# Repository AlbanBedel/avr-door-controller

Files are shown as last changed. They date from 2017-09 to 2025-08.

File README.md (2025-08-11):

# AVR based wiegand door controller

This project is about building an open source physical access control
system for small communities and groups.

## Electronic

In this directory you will find the hardware design (schematics and PCB) for
a two door controller using an Arduino Nano. Its main features are:

* Can be powered with 12V or 24V.
* Support various setup for the door lock, the relay can be connected to
  12V, 24V or GND as normally open or as normally closed.
* An USB power supply to power additional devices such as an AP for network
  connectivity.
* Use RJ-45 connectors for the doors to allow standardizing the physical
  installation.

This design intentionally doesn't provide network connectivity for two reasons.
First we want to keep the device as cheap and reliable as possible. But most
importantly we want a secure system, implementing secure communication (SSL)
on a small micro-controller is not really possible. So instead of using dubious
Ethernet expansion boards we decided to only provide an USB interface and rely
on external devices running a full OS for access over the network.

### Pin out

	Pin | Function | T-568 A      | T-568 B      | Reader
	------------------------------------------------------
	  1 | Beep     | White Green  | White Orange | Yellow
	  2 | LED      | Green        | Orange       | Blue
	  3 | Status   | White Orange | White Green  |
	  4 | D1       | Blue         | Blue         | White
	  5 | D0       | White Blue   | White Blue   | Green
	  6 | Relay    | Orange       | Green        |
	  7 | 12V      | White Brown  | White Brown  | Red
	  8 | GND      | Brown        | Brown        | Black

## Firmware

In this directory you will find the firmware for the above hardware,
it supports both the Arduino Nano version 2 and version 3. We recommend using
version 3 as they have a much large EEPROM which allow for up to 200 access
records.

The firmware currently support:

* 26 bits wiegand RFID readers
* RFID reader with keypad for PIN
* Access with PIN only, card only or card + PIN
* TOTP and HOTP PIN
* Simple access records management over USB

The following is planned:

* Support external EEPROM for more access records
* 34 bits RFID cards

## Daemon

In this directory you will find a daemon that allow managing one or more
controllers using OpenWrt ubus. As OpenWrt include a JSON-RPC interface to ubus
this daemon allow to manage the controllers over the network using a JSON-RPC
interface.

## Client

In this directory you will find the client software to manage the controllers.
First is a tool (and python API) that allow to manage a controller, either over
USB or over JSON-RPC. This tool is pretty low level but make it easy to setup
a single controller with a couple of users. Then there is database backed tool
that allow to easily manage larger deployments with several controllers and many
users.

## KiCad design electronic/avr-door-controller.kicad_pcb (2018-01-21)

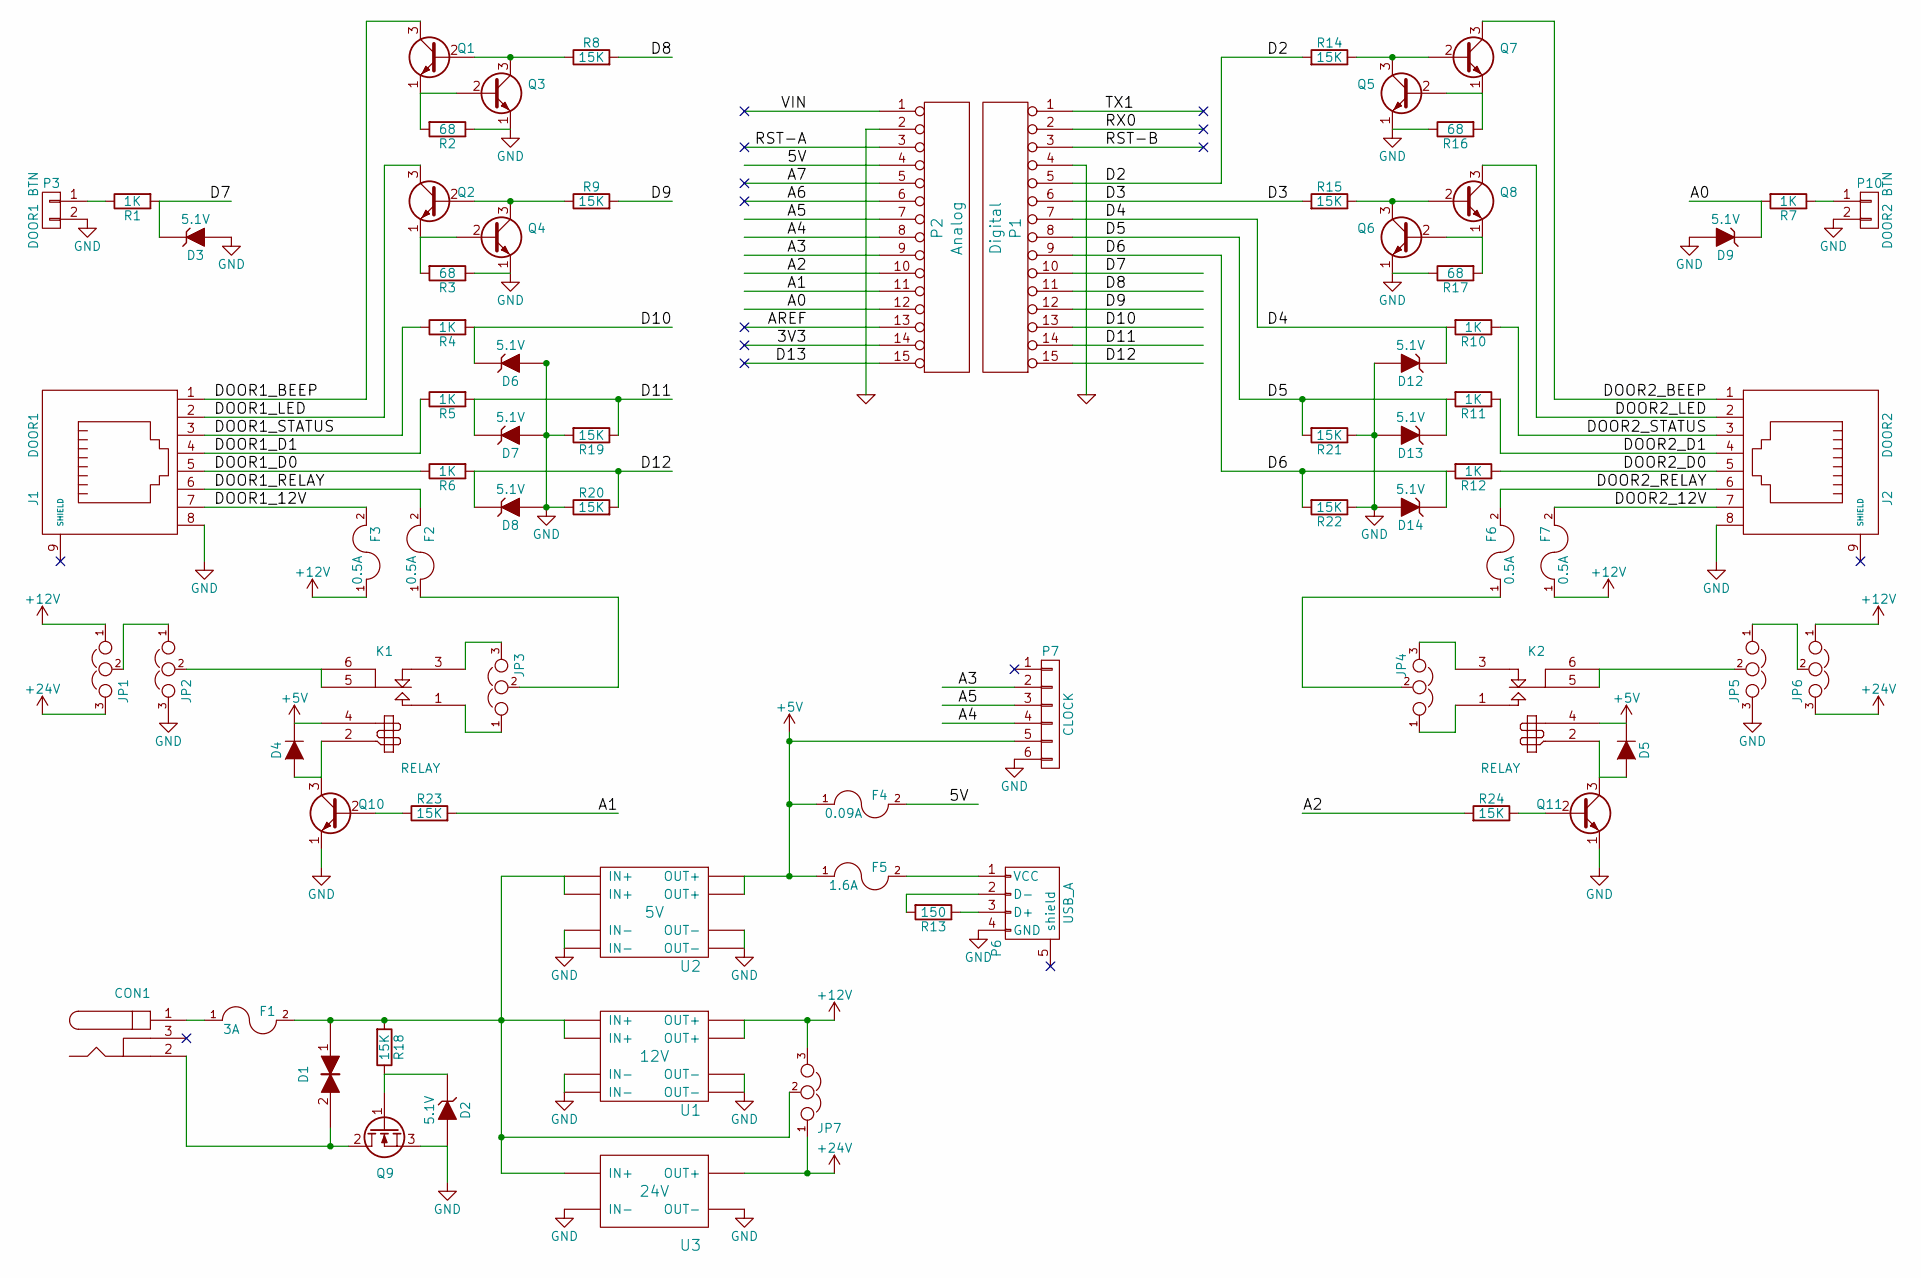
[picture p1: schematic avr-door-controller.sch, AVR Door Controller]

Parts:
CON1: 24V; BARREL_JACK; Mouser Part No 490-PJ-002BH
D1: TVS; Diode_DO-41_SOD81_Vertical_AnodeUp; Mouser Part No 750-P4KE30CA-G
D2: 5.1V; Diode_DO-35_SOD27_Horizontal_RM10
D3, D6, D7, D8, D9, D12, D13, D14: 5.1V; Diode_DO-35_SOD27_Horizontal_RM10; Part 1N5231B
D4, D5: 1N4148; Diode_DO-35_SOD27_Horizontal_RM10
F1: 3A; Bourns_PPTC_Style_2; Mouser Part No 652-MFR300
F2: 0.5A; Bourns_PPTC_Style_1; Mouser Part No 530-0ZRC0050FF1E
F3, F6, F7: 0.5A; Bourns_PPTC_Style_1
F4: 0.09A; Bourns_PPTC_Style_1; Mouser Part No 530-0ZRC0015FF1E
F5: 1.6A; Bourns_PPTC_Style_1; Mouser Part No 650-RUEF160-2
J1: DOOR1; RJ45_8; Mouser Part No 649-54602-908LF
J2: DOOR2; RJ45_8
JP1: 12V|24V; PINHEAD1-3; Mouser Part No 538-22-28-4030
JP2, JP5: VCC|GND; PINHEAD1-3
JP3, JP4: NC | NO; PINHEAD1-3
JP6, JP7: 12V|24V; PINHEAD1-3
K1, K2: RELAY; JRC-21F
P1: Digital; Socket_Strip_Arduino_1x15; Mouser Part No 992-15FX1-254MM
P2: Analog; Socket_Strip_Arduino_1x15; Mouser Part No 992-15FX1-254MM
P3: DOOR1 BTN; bornier2; Mouser Part No 504-EM367502
P6: USB_A; Mouser Part No 706-33UBAR-04SW11
P7: CLOCK; PINHEAD1-6; Mouser Part No 855-M20-9990646
P10: DOOR2 BTN; bornier2
Q1, Q3, Q5, Q7: Q_NPN_EBC; TO-92_Inline_Narrow_Oval
Q2, Q10, Q11: Q_NPN_EBC; TO-92_Inline_Narrow_Oval; Part 2N3904; Mouser Part No 833-2N3904-AP
Q4, Q6, Q8: Q_NPN_EBC; TO-92_Inline_Narrow_Oval; Part 2N3904
Q9: Q_NMOS_GDS; TO-251AA; Mouser Part No 942-IRFU7546PBF
R1, R5, R6, R7, R10, R11, R12: 1K; Resistor_Horizontal_RM10mm
R2: 68; Resistor_Horizontal_RM10mm; Mouser Part No 71-CCF0768R0GKE36
R3, R16, R17: 68; Resistor_Horizontal_RM10mm
R4: 1K; Resistor_Horizontal_RM10mm; Mouser Part No 594-SFR25H0001001JA5
R8, R23, R24: 15K; Resistor_Horizontal_RM10mm; Mouser Part No 603-MFR-25FBF52-15K
R9, R14, R15, R18, R19, R20, R21, R22: 15K; Resistor_Horizontal_RM10mm
R13: 150; Resistor_Horizontal_RM10mm; Mouser Part No 603-MFR-25FBF52-150R
U1: 12V; XM1584
U2: 5V; XM1584
U3: 24V; MT3608

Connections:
+5V: D4.1 (K), D5.1 (K), F4.1, F5.1, K1.4, K2.4, P7.5, U2.7 (OUT+), U2.8 (OUT+)
+12V: F3.1, F7.1, JP1.1, JP6.1, JP7.3, U1.7 (OUT+), U1.8 (OUT+)
+24V: JP1.3, JP6.3, JP7.1, U3.4 (OUT+)
/3V3: P2.14
/5V: F4.2, P2.4
/A0: D9.1 (K), P2.12, R7.2
/A1: P2.11, R23.2
/A2: P2.10, R24.2
/A3: P2.9, P7.2
/A4: P2.8, P7.4
/A5: P2.7, P7.3
/A6: P2.6
/A7: P2.5
/AREF: P2.13
/D2: P1.5, R14.2
/D3: P1.6, R15.2
/D4: D12.1 (K), P1.7, R10.2
/D5: D13.1 (K), P1.8, R11.2, R21.2
/D6: D14.1 (K), P1.9, R12.2, R22.2
/D7: D3.1 (K), P1.10, R1.2
/D8: P1.11, R8.2
/D9: P1.12, R9.2
/D10: D6.1 (K), P1.13, R4.2
/D11: D7.1 (K), P1.14, R5.2, R19.1
/D12: D8.1 (K), P1.15 (p15), R6.2, R20.2
/D13: P2.15 (p15)
/DOOR1_12V: F3.2, J1.7
/DOOR1_BEEP: J1.1, Q1.3 (C)
/DOOR1_D0: J1.5, R6.1
/DOOR1_D1: J1.4, R5.1
/DOOR1_LED: J1.2, Q2.3 (C)
/DOOR1_RELAY: F2.2, J1.6
/DOOR1_STATUS: J1.3, R4.1
/DOOR2_12V: F7.2, J2.7
/DOOR2_BEEP: J2.1, Q7.3 (C)
/DOOR2_D0: J2.5, R12.1
/DOOR2_D1: J2.4, R11.1
/DOOR2_LED: J2.2, Q8.3 (C)
/DOOR2_RELAY: F6.2, J2.6
/DOOR2_STATUS: J2.3, R10.1
/RST-A: P2.3
/RST-B: P1.3
/RX0: P1.2
/TX1: P1.1
/VIN: P2.1
GND: D2.2 (A), D3.2 (A), D6.2 (A), D7.2 (A), D8.2 (A), D9.2 (A), D12.2 (A), D13.2 (A), D14.2 (A), J1.8, J2.8, JP2.3, JP5.3, P1.4, P2.2, P3.2, P6.4 (GND), P7.6, P10.2, Q3.1 (E), Q4.1 (E), Q5.1 (E), Q6.1 (E), Q9.3 (S), Q10.1 (E), Q11.1 (E), R2.1, R3.1, R16.1, R17.1, R19.2, R20.1, R21.1, R22.1, U1.3 (IN-), U1.4 (IN-), U1.5 (OUT-), U1.6 (OUT-), U2.3 (IN-), U2.4 (IN-), U2.5 (OUT-), U2.6 (OUT-), U3.1 (IN-), U3.3 (OUT-)
unnamed: CON1.1, F1.1
unnamed: CON1.2, D1.2, Q9.2 (D)
unnamed: D1.1, F1.2, JP7.2, R18.2, U1.1 (IN+), U1.2 (IN+), U2.1 (IN+), U2.2 (IN+), U3.2 (IN+)
unnamed: D2.1 (K), Q9.1 (G), R18.1
unnamed: D4.2 (A), K1.2, Q10.3 (C)
unnamed: D5.2 (A), K2.2, Q11.3 (C)
unnamed: F2.1, JP3.2
unnamed: F5.2, P6.1 (VCC)
unnamed: F6.1, JP4.2
unnamed: JP1.2, JP2.1
unnamed: JP2.2, K1.5 (C1), K1.6
unnamed: JP3.1, K1.1 (T1)
unnamed: JP3.3, K1.3 (R1)
unnamed: JP4.1, K2.1 (T1)
unnamed: JP4.3, K2.3 (R1)
unnamed: JP5.1, JP6.2
unnamed: JP5.2, K2.5 (C1), K2.6
unnamed: P3.1, R1.1
unnamed: P6.2 (D-), R13.2
unnamed: P6.3 (D+), R13.1
unnamed: P10.1, R7.1
unnamed: Q1.1 (E), Q3.2 (B), R2.2
unnamed: Q1.2 (B), Q3.3 (C), R8.1
unnamed: Q2.1 (E), Q4.2 (B), R3.2
unnamed: Q2.2 (B), Q4.3 (C), R9.1
unnamed: Q5.2 (B), Q7.1 (E), R16.2
unnamed: Q5.3 (C), Q7.2 (B), R14.1
unnamed: Q6.2 (B), Q8.1 (E), R17.2
unnamed: Q6.3 (C), Q8.2 (B), R15.1
unnamed: Q10.2 (B), R23.1
unnamed: Q11.2 (B), R24.1

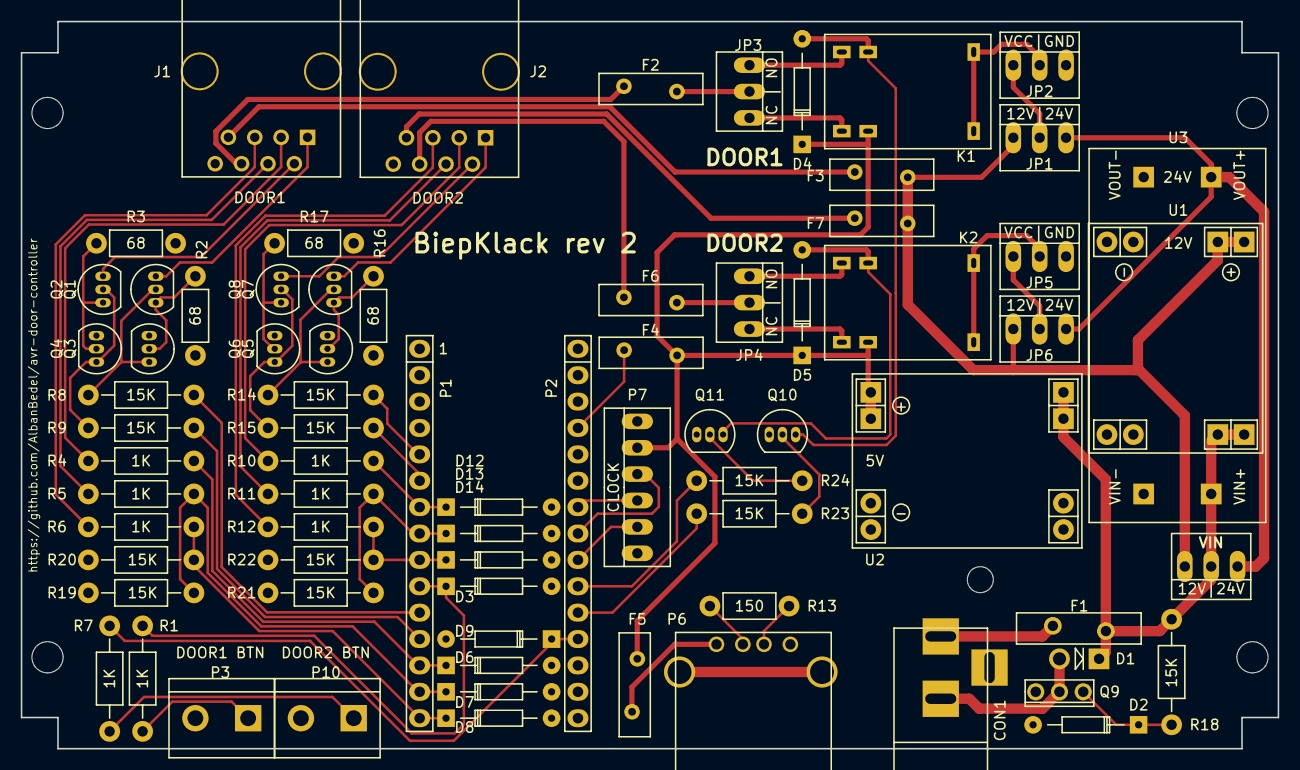
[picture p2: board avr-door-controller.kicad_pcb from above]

Board: 2 copper layers, 121.0 x 70.0 mm, 75 parts (0 on the bottom side), 67 nets.

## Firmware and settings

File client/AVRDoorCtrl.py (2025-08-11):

#!/usr/bin/env python3

import serial
import struct
import crcmod
import ubus
import json
import time
import calendar
import logging
import functools
import base64
from urllib.parse import urldefrag

try:
    from Cryptodome.Hash import HMAC, SHA1
except ModuleNotFoundError:
    HMAC = None
    SHA1 = None

class AVRDoorCtrlUartTransport(object):
    """
    Implement send and receiving messages over a serial port.
    The messages are transmitted using the following format:

      STE CMD LENGTH PAYLOAD CRC

    where
      STE:	Start byte (\x7e)
      CMD:	Command type (uint8_t)
      LENGTH:	Length of payload (uint8_t)
      CRC:	Xmodem CRC of the CMD-LENGTH-PAYLOAD (uint16_t le)

    Furthermore all the data after the start byte is escaped using:
       0x7E <-> 0x7D 0x5E
       0x7D <-> 0x7D 0x5D
    """
    def __init__(self, port, timeout=5):
        self._tty = serial.Serial(port, 38400, timeout=timeout)

    @staticmethod
    def compute_crc(data):
        crc = crcmod.predefined.Crc('xmodem')
        crc.update(data)
        return crc.crcValue

    @classmethod
    def escape_msg(cls, msg):
        return msg.replace(b'\x7d', b'\x7d\x5d').replace(b'\x7e', b'\x7d\x5e')

    @classmethod
    def unescape_msg(cls, msg):
        return msg.replace(b'\x7d\x5e', b'\x7e').replace(b'\x7d\x5d', b'\x7d')

    def read_msg(self):
        sync = False
        escape = False
        type = None
        length = None
        data = b''
        pos = 0
        crc = None

        while True:
            c = self._tty.read(1)
            if len(c) < 1:
                raise TimeoutError
            c = c[0]
            if c == 0x7E:
                sync = True
                escape = False
                type = None
                length = None
                continue

            # Skip everything until we sync
            if sync != True:
                continue

            # Handle escaped bytes
            if escape == True:
                c ^= 0x20
                escape = False
            elif c == 0x7D:
                escape = True
                continue

            # Read the message type
            if type == None:
                type = c
                continue

            # Read the payload size
            if length == None:
                length = c
                continue

            # Read the payload
            if pos < length:
                data += struct.pack("B", c)
                pos += 1
                continue

            # Read the first CRC byte
            if crc == None:
                crc = c
                continue

            # Read the second CRC byte
            crc |= c << 8

            # Check the CRC
            data_crc = self.compute_crc(struct.pack("BB", type, length) + data)
            if crc != data_crc:
                raise ValueError

            return type, data

    def send_msg(self, type, payload = None):
        # Get and check the payload size
        if payload != None:
            length = len(payload)
            if length > 255:
                raise ValueError
        else:
            length = 0
            payload = b''
        # Assemble the message
        pkt = struct.pack("BB", type, length) + payload
        pkt += struct.pack("<H", self.compute_crc(pkt))
        # Format the packet
        pkt = b'\x7e' + self.escape_msg(pkt)
        # And send it out
        self._tty.write(pkt)

class AVRDoorCtrlError(Exception):
    EPERM = 1
    ENOENT = 2
    EINTR = 4
    EIO = 5
    E2BIG = 7
    ENOMEM = 12
    EFAULT = 14
    EBUSY = 16
    EEXIST = 17
    ENODEV = 19
    EINVAL = 22
    ENOSPC = 28
    ERANGE = 34

    _errors = {
        EPERM: "Operation not permitted",
        ENOENT: "No such file or directory",
        EINTR: "Interrupted system call",
        EIO: "I/O error",
        E2BIG: "Argument list too long",
        ENOMEM: "Out of memory",
        EFAULT: "Bad address",
        EBUSY: "Device or resource busy",
        EEXIST: "File exists",
        ENODEV: "No such device",
        EINVAL: "Invalid argument",
        ENOSPC: "No space left on device",
        ERANGE: "Out of range",
    }

    def __init__(self, errno):
        self.errno = errno

    @classmethod
    def strerror(cls, errno):
        return cls._errors.get(errno, f"Error {errno}")

    def __str__(self):
        return self.strerror(self.errno)

class AVRDoorCtrlSerialHandler(object):
    CMD_GET_DEVICE_DESCRIPTOR = 0
    CMD_GET_TIME = 2
    CMD_SET_TIME = 3
    CMD_GET_CONTROLLER_CONFIG = 4
    CMD_SET_CONTROLLER_CONFIG = 5
    CMD_GET_DOOR_CONFIG = 10
    CMD_SET_DOOR_CONFIG = 11
    CMD_GET_ACCESS_RECORD = 20
    CMD_SET_ACCESS_RECORD = 21
    CMD_SET_ACCESS = 22
    CMD_REMOVE_ALL_ACCESS = 23
    CMD_GET_ACCESS = 24
    CMD_GET_USED_ACCESS = 25
    CMD_GET_ACCESS_RECORD_V2 = 30
    CMD_SET_ACCESS_RECORD_V2 = 31
    CMD_SET_ACCESS_V2 = 32
    CMD_GET_ACCESS_V2 = 33
    CMD_GET_USED_ACCESS_V2 = 34

    EVENT_BASE = 127
    EVENT_STARTED = EVENT_BASE + 0
    EVENT_ACCESS = EVENT_BASE + 1
    EVENT_DOOR_STATUS = EVENT_BASE + 2

    REPLY_OK = 0
    REPLY_ERROR = 255

    access_record_types = ("none", "pin", "card", "card+pin")

    ACCESS_TYPE_NONE = 0
    ACCESS_TYPE_PIN = 1
    ACCESS_TYPE_CARD = 2
    ACCESS_TYPE_CARD_AND_PIN = ACCESS_TYPE_CARD | ACCESS_TYPE_PIN

    ACCESS_RECORD_TYPE_CARD_NONE = 0
    ACCESS_RECORD_TYPE_CARD_ID = 1

    ACCESS_RECORD_TYPE_PIN_NONE = 0
    ACCESS_RECORD_TYPE_PIN_FIXED = 1 << 1
    ACCESS_RECORD_TYPE_PIN_HOTP = 2 << 1
    ACCESS_RECORD_TYPE_PIN_TOTP = 3 << 1

    CONTROLLER_KEY_SIZE = 20

    @staticmethod
    def parse_version(version):
        major, minor = version.split('.')
        return int(major) * 1000 + int(minor)

    def __init__(self, dev, *args, controller_version = None, **kwargs):
        self._events = []
        self._descriptor = None
        if dev.startswith('/dev/tty'):
            self._transport = AVRDoorCtrlUartTransport(dev, *args, **kwargs)
        else:
            raise ValueError
        try:
            type, payload = self.read_msg()
            if type != self.EVENT_STARTED:
                raise TypeError("Initial event is not a start event")

            if len(payload) > 0:
                self._descriptor = self.unpack_device_descriptor(payload)
                version = self._descriptor['version']
            else:
                # Version 0.2 doesn't send the device descriptor at start
                version = '0.2'
        except TimeoutError:
            # Version 0.1 doesn't send a start event at all
            version = '0.1'
        except:
            raise

        logging.info(f"Device version {version} started")
        if controller_version is not None:
            logging.warning(f"Forcing controller version {controller_version}")
            version = controller_version
        self._version = self.parse_version(version)

    @staticmethod
    def since_version(version):
        def decorator(version, method):
            @functools.wraps(method)
            def wrapper(self, *args, **kwargs):
                if self._version < version:
                    raise NotImplementedError
                return method(self, *args, **kwargs)
            return wrapper
        return functools.partial(decorator, version)

    def read_msg(self):
        type, payload = self._transport.read_msg()
        logging.debug("Got %02x - %s" % (type, ":".join("{:02x}".format(c) for c in payload)))
        return type, payload

    def read_event(self):
        if len(self._events) > 0:
            type, payload = self._events.pop(0)
        else:
            type, payload = self.read_msg()
        return self.parse_event(type, payload)

    def send_msg(self, type, payload = None):
        desc = (" - " + ":".join("{:02x}".format(c) for c in payload)) \
            if payload is not None else ""
        logging.debug("Send: %02x%s" % (type, desc))
        self._transport.send_msg(type, payload)

    def send_cmd(self, type, payload = None, response_size=0):
        self.send_msg(type, payload)
        # Read the incoming messages, but queue the events
        while True:
            reply, response = self.read_msg()
            if self.is_event(reply):
                self._events.append((reply, response))
            else:
                break
        # Raise errors
        if reply == self.REPLY_ERROR:
            if len(response) < 1:
                raise Exception("Invalid error reply")
            errno, = struct.unpack("b", response)
            raise AVRDoorCtrlError(-errno)
        # Make sure we got an OK
        if reply != self.REPLY_OK:
            raise Exception("Bad reply type: %d" % reply)
        # Make sure we got enough data
        if len(response) < response_size:
            raise Exception("Bad response length: %d" % len(response))
        return response

    @classmethod
    def is_event(cls, type):
        return type >= cls.EVENT_BASE and type < cls.REPLY_ERROR

    @staticmethod
    def pack_pin(pin):
        val = 0xFFFFFFFF
        for c in pin:
            val = ((val << 4) & 0xFFFFFFFF) | int(c, 10)
        return val

    @staticmethod
    def unpack_pin(pin):
        s = ''
        for i in range(7, -1, -1):
            d = (pin >> (i * 4)) & 0xF
            if d != 0xF:
                s += '%d' % d
        return s

    @staticmethod
    def unpack_device_descriptor(response):
        major, minor, doors, records = struct.unpack("<BBBH", response[0:5])
        ret = {
            "version": "%d.%d" % (major, minor),
            "num_doors": doors,
            "num_access_records" : records,
        }
        if len(response) > 5:
            ret["free_access_records"], = struct.unpack("<H", response[5:7])
        return ret

    def get_device_descriptor(self):
        if self._descriptor:
            return self._descriptor
        response = self.send_cmd(
            self.CMD_GET_DEVICE_DESCRIPTOR, None, 5)
        return self.unpack_device_descriptor(response)

    def get_controller_config(self):
        response = self.send_cmd(
            self.CMD_GET_CONTROLLER_CONFIG, None,
            self.CONTROLLER_KEY_SIZE)
        key = response[0:20]
        ret = {
            "key": base64.b16encode(key).decode('ascii'),
        }
        return ret

    def set_controller_config(self, root_key=None):
        if root_key is not None:
            key = base64.b16decode(root_key).zfill(self.CONTROLLER_KEY_SIZE)
            key = key[:self.CONTROLLER_KEY_SIZE]
        else:
            key = b'\x00' * self.OTP_KEY_SIZE
        self.send_cmd(self.CMD_SET_CONTROLLER_CONFIG, key)
        return {}

    def get_door_config(self, index):
        response = self.send_cmd(self.CMD_GET_DOOR_CONFIG,
                                 struct.pack("<B", int(index)), 7)
        open_time, = struct.unpack("<H", response[0:2])
        ret = {
            "open_time": open_time,
        }
        return ret

    def set_door_config(self, index, open_time):
        req = struct.pack("<BHHHB", int(index), int(open_time), 0, 0, 0)
        self.send_cmd(self.CMD_SET_DOOR_CONFIG, req)
        return {}

    @classmethod
    def _unpack_access_record(self, response, pin = None, card = None):
        key, access = struct.unpack("<LB", response[0:5])
        # If the record is invalid ignore it
        if access & (1 << 2):
            access = 0
        type = access & 0x3
        doors = (access >> 4) & 0xF
        ret = {
            "used": bool(access & (1 << 3)),
        }
        if type != self.ACCESS_TYPE_NONE:
            ret['doors'] = doors
        if type == self.ACCESS_TYPE_PIN:
            ret['pin'] = self.unpack_pin(key)
        elif type == self.ACCESS_TYPE_CARD:
            ret['card'] = key
        elif type == self.ACCESS_TYPE_CARD_AND_PIN:
            if pin != None:
                ret['pin'] = pin
                ret['card'] = key ^ self.pack_pin(pin)
            elif card != None:
                ret['pin'] = self.unpack_pin(key ^ int(card))
                ret['card'] = card
            else:
                ret['card+pin'] = key
        return ret

    def get_access_record(self, index, pin = None, card = None):
        response = self.send_cmd(self.CMD_GET_ACCESS_RECORD,
                                 struct.pack("<H", int(index)), 5)
        ret = self._unpack_access_record(response, pin, card)
        ret['index'] = index
        return ret

    @classmethod
    def _unpack_access_record_v2(self, response):
        hdr, card, pin = struct.unpack("<BLL", response[0:9])
        ret = {
            "doors": (hdr >> 4) & 0xF,
            "used": bool(hdr & (1 << 3)),
        }

        card_type = hdr & 1
        if card_type == self.ACCESS_RECORD_TYPE_CARD_ID:
            ret['card_type'] = 'id'
            ret['card'] = card

        pin_type = hdr & (3 << 1)
        if pin_type == self.ACCESS_RECORD_TYPE_PIN_FIXED:
            ret['pin_type'] = 'fixed'
            ret['pin'] = self.unpack_pin(pin)
        elif pin_type in (self.ACCESS_RECORD_TYPE_PIN_HOTP,
                          self.ACCESS_RECORD_TYPE_PIN_TOTP):
            ret['pin_type'] = 'hotp' \
                if pin_type == self.ACCESS_RECORD_TYPE_PIN_HOTP \
                else 'totp'
            ret['otp_key'] = pin & 0x3FF
            ret['otp_digits'] = ((pin >> 10) & 3) + 6
            if pin_type == self.ACCESS_RECORD_TYPE_PIN_HOTP:
                ret['hotp_resync_limit'] = (pin >> 12) & 0xF
                ret['hotp_counter'] = (pin >> 16) & 0xFFFF
            else:
                ret['totp_allow_followings'] = (pin >> 12) & 3
                ret['totp_allow_previous'] = (pin >> 14) & 3
                ret['totp_interval'] = (pin >> 16) & 0xFFFF

        return ret

    @since_version(3)
    def get_access_record_v2(self, index):
        response = self.send_cmd(self.CMD_GET_ACCESS_RECORD_V2,
                                 struct.pack("<H", int(index)), 5)
        ret = self._unpack_access_record_v2(response)
        ret['index'] = index
        return ret

    @classmethod
    def _pack_access_record(self, pin = None, card = None,
                            doors = 0, used = False, card_pin = None):
        if card_pin != None:
            type = self.ACCESS_TYPE_CARD_AND_PIN
            key = int(card_pin)
        elif pin != None and card != None:
            type = self.ACCESS_TYPE_CARD_AND_PIN
            key = int(card) ^ self.pack_pin(str(pin))
        elif card != None:
            type = self.ACCESS_TYPE_CARD
            key = int(card)
        elif pin != None:
            type = self.ACCESS_TYPE_PIN
            key = self.pack_pin(str(pin))
        else:
            type = self.ACCESS_TYPE_NONE
            key = 0
        access = type | ((bool(int(used)) & 1) << 3) | ((int(doors) & 0xF) << 4)
        return struct.pack("<LB", key, access)

    def set_access_record(self, index, pin = None, card = None,
                          used = False, doors = 0, **kwargs):
        req = struct.pack("<H", index)
        req += self._pack_access_record(pin, card, doors, used,
                                        kwargs.get('card+pin'))
        self.send_cmd(self.CMD_SET_ACCESS_RECORD, req, 0)
        return {}

    def set_access(self, pin = None, card = None, doors = 0):
        if pin == None and card == None:
            raise ValueError('No card number or pin given')
        req = self._pack_access_record(pin, card, doors)
        self.send_cmd(self.CMD_SET_ACCESS, req, 0)
        return {}

    @classmethod
    def _pack_access_record_v2_type(self, card_type, pin_type):
        rec_type = 0

        if card_type is None:
            pass
        elif card_type == 'id':
            rec_type |= self.ACCESS_RECORD_TYPE_CARD_ID
        else:
            raise ValueError('Invalid card type')

        if pin_type is None:
            pass
        elif pin_type == 'fixed':
            rec_type |= self.ACCESS_RECORD_TYPE_PIN_FIXED
        elif pin_type == 'hotp':
            rec_type |= self.ACCESS_RECORD_TYPE_PIN_HOTP
        elif pin_type == 'totp':
            rec_type |= self.ACCESS_RECORD_TYPE_PIN_TOTP
        else:
            raise ValueError('Invalid pin type')

        if rec_type == 0:
            raise ValueError('No card or pin given')

        return rec_type

    @classmethod
    def _pack_access_record_v2(self, card_type = None, pin_type = None,
                               doors = 0, used = False, card = None,
                               pin = None, otp_key = None,
                               otp_digits = 6, hotp_resync_limit = 1,
                               hotp_counter = 0, totp_interval = 60,
                               totp_allow_followings = 0,
                               totp_allow_previous = 0):
        if pin_type in ('totp', 'hotp'):
            if otp_digits < 6 or otp_digits > 10:
                raise ValueError('OTP digits must be between 6 and 10')
        if pin_type == 'totp':
            if totp_allow_followings < 0 or totp_allow_followings > 3:
                raise ValueError('TOTP allow followings must be between 0 and 3')
            if totp_allow_previous < 0 or totp_allow_previous > 3:
                raise ValueError('TOTP allow previous must be between 0 and 3')
            if totp_interval < 0:
                raise ValueError('TOTP interval must be >= 0')
        if pin_type == 'hotp':
            if hotp_resync_limit < 0 or hotp_resync_limit > 15:
                raise ValueError('HOTP resync limit must be between 0 and 15')
            if hotp_counter < 0:
                raise ValueError('HOTP counter must be >= 0')

        hdr = self._pack_access_record_v2_type(card_type, pin_type)
        hdr |= (bool(used) << 3) | ((int(doors) & 0xF) << 4)
        rec_hdr = struct.pack("B", hdr)

        if card_type is None:
            rec_card = struct.pack("<L", 0)
        elif card_type == 'id':
            rec_card = struct.pack("<L", int(card))
        else:
            raise ValueError('Invalid card type')

        if pin_type is None:
            rec_pin = struct.pack("<L", 0)
        elif pin_type == 'fixed':
            rec_pin = struct.pack("<L", self.pack_pin(str(pin)))
        elif pin_type in ('hotp', 'totp'):
            otp_cfg = otp_key & 0x3FF
            otp_cfg |= ((otp_digits - 6) & 3) << 10
            if pin_type == 'totp':
                otp_cfg |= (totp_allow_followings & 3) << 12
                otp_cfg |= (totp_allow_previous & 3) << 14
                c = totp_interval
            if pin_type == 'hotp':
                otp_cfg |= (hotp_resync_limit & 0xF) << 12
                c = hotp_counter
            rec_pin = struct.pack("<HH", otp_cfg, c)
        else:
            raise ValueError('Invalid PIN type')

        return rec_hdr + rec_card + rec_pin

    @since_version(3)
    def set_access_record_v2(self, index, **kwargs):
        req = struct.pack("<H", index)
        req += self._pack_access_record_v2(**kwargs)
        self.send_cmd(self.CMD_SET_ACCESS_RECORD_V2, req, 0)
        return {}

    @since_version(3)
    def set_access_v2(self, **kwargs):
        req = self._pack_access_record_v2(**kwargs)
        self.send_cmd(self.CMD_SET_ACCESS_V2, req, 0)
        return {}

    def get_access(self, pin = None, card = None):
        if pin == None and card == None:
            raise ValueError('No card number or pin given')
        req = self._pack_access_record(pin, card)
        response = self.send_cmd(self.CMD_GET_ACCESS, req, 1)
        return {
            'doors': struct.unpack('B', response[0:1])[0],
        }

    @classmethod
    def _pack_get_access_req_v2(self, card_type = None, pin_type = None,
                                card = None, pin = None, otp_key = None,
                                **kwargs):

        req_type = self._pack_access_record_v2_type(card_type, pin_type)

        if card_type is None:
            req_card = 0
        elif card_type == 'id':
            req_card = int(card)
        else:
            raise ValueError('Invalid card type')

        if pin_type is None:
            req_pin = 0
        elif pin_type == 'fixed':
            req_pin = self.pack_pin(pin)
        elif pin_type in ('totp', 'hotp'):
            req_pin = int(otp_key)
        else:
            raise ValueError('Invalid pin type')

        return struct.pack('<BLL', req_type, req_card, req_pin)

    @since_version(3)
    def get_access_v2(self, **kwargs):
        req = self._pack_get_access_req_v2(**kwargs)
        response = self.send_cmd(self.CMD_GET_ACCESS_V2, req, 1)
        return self._unpack_access_record_v2(response)

    def remove_all_access(self):
        self.send_cmd(self.CMD_REMOVE_ALL_ACCESS)
        return {}

    def _generate_used_access(self, clear):
        i = 0
        while True:
            req = struct.pack("<HB", int(i), clear)
            response = self.send_cmd(self.CMD_GET_USED_ACCESS, req, 7)
            i, = struct.unpack("<H", response[0:2])
            rec = self._unpack_access_record(response[2:])
            if 'doors' not in rec:
                return
            rec['index'] = i
            yield rec
            i = i + 1

    def get_used_access(self, clear = False):
        return {
            'used': list(self._generate_used_access(clear)),
        }

    def _generate_used_access_v2(self, clear):
        i = 0
        while True:
            req = struct.pack("<HB", int(i), clear)
            try:
                response = self.send_cmd(self.CMD_GET_USED_ACCESS_V2, req, 11)
            except AVRDoorCtrlError as err:
                if err.errno == AVRDoorCtrlError.ENOENT:
                    return
                raise
            i, = struct.unpack("<H", response[0:2])
            rec = self._unpack_access_record_v2(response[2:])
            rec['index'] = i - 1
            yield rec
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

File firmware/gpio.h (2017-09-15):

/*
 * Copyright 2014  Alban Bedel (alban.bedel@avionic-design.de)
 *
 * This program is free software; you can redistribute it and/or modify
 * it under the terms of the GNU General Public License as published by
 * the Free Software Foundation, either version 3 of the License, or
 * (at your option) any later version.
 */
#ifndef GPIO_H
#define GPIO_H

/** \defgroup GPIO GPIO
 *
 * The GPIO API provides an abstraction of the pins access similar
 * to the Linux GPIO API.
 *
 * @{
 */

#include <stdint.h>

/** \defgroup GPIOPort GPIO Ports
 * @{
 */
#define GPIO_PORT_A		1
#define GPIO_PORT_B		2
#define GPIO_PORT_C		3
#define GPIO_PORT_D		4
#define GPIO_PORT_E		5
#define GPIO_PORT_F		6
/**@}*/

/** \defgroup GPIOPolarity GPIO Polarity
 * @{
 */
#define GPIO_HIGH_ACTIVE	0
#define GPIO_LOW_ACTIVE		1
/**@}*/

/** Generate a GPIO ID from port and pin number
 *
 * \param port GPIO port, one of \ref GPIOPort
 * \param pin Pin number
 * \param pol Pin polarity
 * \return The GPIO ID
 */
#define GPIO_ID(port, pin, pol) \
	((((pol) & 1) << 7) | (((port) & 0xF) << 3) | ((pin) & 0x7))

/** Generate a GPIO ID from a port name and pin number
 *
 * \param port Short port name: A, B, C, etc
 * \param pin Pin number
 * \return The GPIO ID
 *
 * This is a convenience macro to make GPIO definitions nicer when
 * the port is a compile time constant.
 */
#define GPIO(port, pin, pol) \
	GPIO_ID(GPIO_PORT_##port, pin, GPIO_##pol)

/** Get the port from a GPIO ID
 *
 * \param gpio GPIO ID
 * \return Port, one of \ref GPIOPort
 */
#define GPIO_PORT(gpio)		(((gpio) >> 3) & 0xF)

/** Get the pin from a GPIO ID
 *
 * \param gpio GPIO ID
 * \return Pin number
 */
#define GPIO_PIN(gpio)		((gpio) & 0x7)

/** Get the polarity from a GPIO ID
 *
 * \param gpio GPIO ID
 * \return GPIO polarity
 */
#define GPIO_POLARITY(gpio)	(((gpio) >> 7) & 1)

/** Set the polarity of a GPIO ID
 *
 * \param gpio GPIO ID
 * \param pol GPIO Polarity
 * \return GPIO ID with the new polarity
 */
#define GPIO_SET_POLARITY(gpio, pol) \
	(((gpio) & 0x7F) | (((pol) & 1) << 7))

/** Check if a GPIO is valid
 *
 * \param gpio GPIO ID
 * \return > 0 if the GPIO ID is valid, <= 0 otherwise
 */
int8_t gpio_is_valid(uint8_t gpio);

/** Configure a GPIO as input
 *
 * \param gpio GPIO ID
 * \param pull Enable the internal pull-up
 * \return 0 on success, a negative value otherwise
 */
int8_t gpio_direction_input(uint8_t gpio, uint8_t pull);

/** Configure a GPIO as output
 *
 * \param gpio GPIO ID
 * \param val Initial value
 * \return 0 on success, a negative value otherwise
 */
int8_t gpio_direction_output(uint8_t gpio, uint8_t val);

/** Get the current value of an input GPIO
 *
 * \param gpio GPIO ID
 * \return the pin state
 */
int8_t gpio_get_value(uint8_t gpio);

/** Set the value of an output GPIO
 *
 * \param gpio GPIO ID
 * \param state The new pin state
 */
void gpio_set_value(uint8_t gpio, uint8_t state);

/** Configure a GPIO as open collector
 *
 * Note that for this mode can only be used with an *external* pull-up,
 * using the on-chip pull is not supported! Furthermore to change the gpio
 * state \ref gpio_open_collector_set_value must be used instead of
 * \ref gpio_set_value.
 *
 * \param gpio GPIO ID
 * \param val Initial value
 * \return 0 on success, a negative value otherwise
 */
int8_t gpio_open_collector(uint8_t gpio, uint8_t val);

/** Set the value of an open collector GPIO
 *
 * \param gpio GPIO ID
 * \param state The new pin state
 */
void gpio_open_collector_set_value(uint8_t gpio, uint8_t state);

/**@}*/
#endif /* GPIO_H */

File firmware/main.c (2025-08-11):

#include <stdlib.h>
#include <stdio.h>
#include <errno.h>
#include <avr/pgmspace.h>
#include <avr/power.h>
#include <avr/interrupt.h>
#include <avr/boot.h>
#include <util/delay.h>
#include "work-queue.h"
#include "door-controller.h"
#include "external-irq.h"
#include "eeprom.h"
#include "utils.h"
#include "uart.h"
#include "ctrl-cmd.h"
#include "gpio.h"
#include "sleep.h"
#include "i2c.h"
#include "rtc.h"

static int8_t check_key(uint8_t door_id, uint8_t type,
			uint32_t card, uint32_t pin, void *context)
{
	int8_t err = -EPERM;

	err = acl_check_access(type, card, pin, door_id);
	if (DEBUG) {
		static char buffer[40];
		static const char fmt[] PROGMEM =
			"Door %d, %c %010ld -> %sauthorized\r\n";

		snprintf_P(buffer, sizeof(buffer), fmt,
			   door_id, (type == DOOR_CTRL_PIN) ? 'P' : 'C',
			   (type == DOOR_CTRL_PIN) ? pin : card,
			   err ? "un" :"");
		uart_blocking_write(buffer);
	}

	return err;
}

extern const struct door_ctrl_config doors_config[] PROGMEM;
static struct door_ctrl dc[NUM_DOORS];

static int init_doors(void)
{
	int8_t err;
	uint8_t i;

	for (i = 0; i < NUM_DOORS; i++) {
		struct door_config eeprom_cfg;
		struct door_ctrl_config cfg;

		memcpy_P(&cfg, &doors_config[i], sizeof(cfg));
		cfg.check_key = check_key;

		eeprom_get_door_config(i, &eeprom_cfg);
		if (eeprom_cfg.open_time > 0 &&
		    eeprom_cfg.open_time < INT16_MAX / 2)
			cfg.open_time = eeprom_cfg.open_time;

		err = door_ctrl_init(&dc[i], &cfg);
		if (err)
			break;
	}

	return err;
}

int main(void)
{
	struct device_descriptor desc = {};
	int8_t err = 0;

	clock_prescale_set(clock_div_1);
	timers_init();

	if (HAS_I2C)
		err = i2c_init(I2C_MAX_RATE);
	if (!err)
		err = acl_init();
	if (!err)
		err = ctrl_cmd_init();
	if (!err)
		err = init_doors();

	sei();

	if (!err && DS3231_ADDR)
		rtc_ds3231_init(DS3231_ADDR, DS3231_IRQ);

	/* On error turn on the life LED and sleep forwever */
	if (err) {
		gpio_direction_output(LIFE_LED_GPIO, 1);
		sleep_while(1);
	}

	ctrl_cmd_init_device_descriptor(&desc);
	ctrl_send_event(CTRL_EVENT_STARTED, &desc, sizeof(desc));
	work_queue_run(LIFE_LED_GPIO);

	return 0;
}

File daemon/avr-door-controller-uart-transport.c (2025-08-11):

/*
 * Copyright (C) 2017 Alban Bedel <albeu@free.fr>
 *
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
 * This program is distributed in the hope that it will be useful,
 * but WITHOUT ANY WARRANTY; without even the implied warranty of
 * MERCHANTABILITY or FITNESS FOR A PARTICULAR PURPOSE.  See the
 * GNU General Public License for more details.
 */

#include <stdlib.h>
#include <stdbool.h>
#include <errno.h>
#include <unistd.h>
#include <sys/types.h>
#include <sys/stat.h>
#include <sys/ioctl.h>
#include <fcntl.h>
#include <termios.h>

#include <libubox/ulog.h>
#include <libubox/list.h>

#include "avr-door-controller-daemon.h"

/* Message decoder state */
#define AVR_DOOR_CTRL_SYNC			0
#define AVR_DOOR_CTRL_RECV_TYPE			1
#define AVR_DOOR_CTRL_RECV_LENGTH		2
#define AVR_DOOR_CTRL_RECV_PAYLOAD		3
#define AVR_DOOR_CTRL_RECV_CRC			4

#define UART_CTRL_START				0x7E
#define UART_CTRL_ESC				0x7D
#define UART_CTRL_UNESCAPE(x)			((x) ^ 0x20)
#define UART_CTRL_ESCAPE(x)			UART_CTRL_UNESCAPE(x)
#define UART_CTRL_CRC_INIT			0

#define UART_CTRL_BUFFER_SIZE (1 + (sizeof(struct avr_door_ctrl_msg) + 2) * 2)


struct avr_door_ctrl_uart_transport {
	struct avr_door_ctrl_transport transport;

	uint8_t recv_buffer[UART_CTRL_BUFFER_SIZE];
	unsigned int recv_buffer_len;
	unsigned int recv_buffer_pos;

	unsigned int recv_state;
	bool recv_escape;
	unsigned int recv_msg_pos;
	uint16_t recv_crc;

	uint8_t send_buffer[UART_CTRL_BUFFER_SIZE];
	unsigned int send_buffer_len;
	unsigned int send_buffer_pos;
};


static uint16_t crc_update(uint16_t crc, uint8_t data)
{
	int i;

	crc = crc ^ ((uint16_t)data << 8);
	for (i=0; i < 8; i++) {
		if (crc & 0x8000)
			crc = (crc << 1) ^ 0x1021;
		else
			crc <<= 1;
        }

	return crc;
}

static uint16_t msg_compute_crc(
	const struct avr_door_ctrl_msg *msg)
{
	uint16_t crc = UART_CTRL_CRC_INIT;
	int i;

	crc = crc_update(crc, msg->type);
	crc = crc_update(crc, msg->length);
	for (i = 0; i < msg->length; i++)
		crc = crc_update(crc, msg->payload[i]);

	return crc;
}

static int msg_encode_byte(uint8_t *buffer, uint8_t byte)
{
	if (byte == UART_CTRL_START || byte == UART_CTRL_ESC) {
		buffer[0] = UART_CTRL_ESC;
		buffer[1] = UART_CTRL_ESCAPE(byte);
		return 2;
	} else {
		buffer[0] = byte;
		return 1;
	}
}

static int msg_encode(const struct avr_door_ctrl_msg *msg, uint8_t *buffer)
{
	uint16_t crc = UART_CTRL_CRC_INIT;
	int i, pos = 0;

	buffer[pos++] = UART_CTRL_START;

	pos += msg_encode_byte(buffer + pos, msg->type);
	pos += msg_encode_byte(buffer + pos, msg->length);
	for (i = 0; i < msg->length; i++)
		pos += msg_encode_byte(buffer + pos, msg->payload[i]);

	crc = msg_compute_crc(msg);
	pos += msg_encode_byte(buffer + pos, crc);
	pos += msg_encode_byte(buffer + pos, crc >> 8);

	return pos;
}

static int uart_ctrl_transport_recv_byte(
	struct avr_door_ctrl_uart_transport *uart,
	uint8_t byte, struct avr_door_ctrl_msg *msg)
{
	/* Handle start bytes */
	if (byte == UART_CTRL_START) {
		/* Warn the upper layer if there was a transport error */
		int err = uart->recv_state == AVR_DOOR_CTRL_SYNC ?
			-ENODATA : -EPROTO;

		uart->recv_state = AVR_DOOR_CTRL_RECV_TYPE;
		uart->recv_escape = false;
		return err;
	}

	/* While not in sync ignore everything */
	if (uart->recv_state == AVR_DOOR_CTRL_SYNC)
		return -ENODATA;

	/* Unescape */
	if (uart->recv_escape) {
		byte = UART_CTRL_UNESCAPE(byte);
		uart->recv_escape = false;
	} else if (byte == UART_CTRL_ESC) {
		uart->recv_escape = true;
		return -ENODATA;
	}

	switch (uart->recv_state) {
	case AVR_DOOR_CTRL_RECV_TYPE:
		msg->type = byte;
		uart->recv_state = AVR_DOOR_CTRL_RECV_LENGTH;
		return -ENODATA;

	case AVR_DOOR_CTRL_RECV_LENGTH:
		msg->length = byte;
		if (msg->length > 0)
			uart->recv_state = AVR_DOOR_CTRL_RECV_PAYLOAD;
		else
			uart->recv_state = AVR_DOOR_CTRL_RECV_CRC;
		uart->recv_msg_pos = 0;
		uart->recv_crc = 0;
		return -ENODATA;

	case AVR_DOOR_CTRL_RECV_PAYLOAD:
		if (uart->recv_msg_pos < sizeof(msg->payload))
			msg->payload[uart->recv_msg_pos] = byte;
		uart->recv_msg_pos++;

		if (uart->recv_msg_pos >= msg->length) {
			uart->recv_state = AVR_DOOR_CTRL_RECV_CRC;
			uart->recv_msg_pos = 0;
		}
		return -ENODATA;

	case AVR_DOOR_CTRL_RECV_CRC:
		uart->recv_crc |= ((unsigned)byte) << (8 * uart->recv_msg_pos);
		uart->recv_msg_pos++;

		if (uart->recv_msg_pos < sizeof(uart->recv_crc))
			return -ENODATA;
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

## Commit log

2017-04-06 boards: Update the Arduino Nano v2 config
    The lastest prototype finally have the final config, we need to move
    the pins of the second door by one.
2017-04-06 trigger: Skip empty steps instead of using a 0 timeout
    This simplify the process a bit and avoid useless timeouts.
    [trigger.c]
2017-04-06 trigger: Add a missing empty line
    Make the code a bit nicer to the eye.
    [trigger.c]
2017-05-02 build: Fix the CFLAGS to fix EEPROM generation with new gcc versions
    In current gcc version when LTO is enabled we need to add
    -ffat-lto-objects to the CFLAGS for the normal EEPROM section to be
    present in the object files.
2017-05-02 wiegand reader: Make WIEGAND_READER_ERROR an unsigned value
    The negative value for WIEGAND_READER_ERROR produce a warning when
    used in a switch, so replace it with 0xFF.
2017-05-02 wiegand reader: Generate an error when the reader is disconnected
    This allow the controller to know that the reader is missing.
    [wiegand-reader.c]
2017-05-02 door ctrl: Rework the event handling to prevent potential races
    Currently the door controller state is changed from timer handlers.
    This is a problem because they run from interrupt handlers so the
    state might change while we handle an event.
    To prevent this we now generate events from the timeout handler and
    then handle the state change from the event handler. To spare some
    memory we use the same handler as for the wiegand events, so the events
    are added with the wiegand reader as source and not the whole
    controller.
    [door-controller.c, main.c]
2017-05-02 door ctrl: Make the error handling consistent
    When an error occurs always switch to the error state and beep.
    [door-controller.c]
2017-05-02 door ctrl: Add an idle timeout
    Add a timeout to switch back to the IDLE state if no input is entered
    in 10s. This ensure that the users always get a clean state when they
    start using the controller.
2017-05-02 eeprom: Rework the access control list to prepare supporting card with pin
    Replace the single 'pin' field in the access record with a 2 bit type
    field and change the lookup function to directly check for the correct
    door and access type.
    [main.c]
2017-05-02 door ctrl: Add support for card with pin
    Allow using a card instead of the enter button to support card with pin.
    We simply xor the card and pin together to generate the key value.
2017-05-02 boards: Add support for the Arduino Nano V3
    This board is the same as the V2 but with an ATmega328 instead of an
    ATmega168 giving it more memory.
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2017-08-09 eeprom: Rework the eeprom API to allow access without using a record index
    Start moving away from the index based access and use the key type and
    key as index.
    [main.c]
2017-08-09 firmware: Enable -Wall and fix a few harmless warnings
    [door-controller.c, main.c, uart-ctrl-transport.c]
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2017-09-06 electronic: Initial version of the board
    Schematics and PCB in the version sent to aisler for the first 3
    prototypes.
    [avr-door-controller.kicad_pcb, avr-door-controller.sch]
2017-09-06 wiegand-reader: Fix the parity check for 26 bits
    First of all the odd and even parity were inverted, then the parity
    wasn't checked on the correct range. After fixing both problems all
    fobs I have at hand are now working properly.
    [wiegand-reader.c]
2017-09-06 door-ctrl: Set all internal functions static
    A few functions where missing the static modifier, add it.
    [door-controller.c]
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2017-09-15 firmware: Replace the init message with an event
    An event can be read by client without any special case and it spare
    us some memory by removing the strings.
    [main.c]
2017-09-15 firmware: Turn on the LED and go to sleep if the init fails
    There is not much we can do in this case but that should gives the
    user a hint that something is wrong with the controller.
    [main.c]
2017-09-15 daemon: uart transport: Remove the init state
    Earlier version of the firmware printed a welcome message before
    starting the main loop. The init state state just avoided reporting
    this as a protocol error. Now that the firmware use the transport
    protocol for this we don't need to handle the init differently
    anymore.
    [avr-door-controller-uart-transport.c]
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2017-09-15 electronic: Increase the revision of the schematics and pcb
    Let's start with the next hardware revision.
    [avr-door-controller.kicad_pcb, avr-door-controller.sch]
2017-09-15 electronic: pcb: Platte the mounting holes of the USB connector
    For some reason I removed the platting on the mounting holes of the
    USB connector. This prevent properly soldering the connector, so set
    the platting back.
    [avr-door-controller.kicad_pcb]
2017-09-15 electronic: Add pull-down on the wiegand D0 and D1 pins
    As the wiegand reader is supposed to pull-up both data lines this
    should allow us to detect if the reader is not connected.
    [avr-door-controller.kicad_pcb, avr-door-controller.sch]
2017-09-15 firmware: gpio: Make the polarity part of the GPIO ID
    Currently we need to have a 'low_active' field next to most gpio, this
    take some RAM and code as each user reimplement xor'ing the low_active
    field with the GPIO value.
    To fix this we now make the polarity part of the GPIO ID, in this way
    the GPIO code can internally take care of this. That reduce the RAM
    usage as we get rid of all the low_active fields and code size as we
    spare various extra xor.
    [arduino_nano_v2.c, atmega168.c, atmega168.h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]
2017-09-15 electronic: Fix the missing power input on the +5V regulator
    Somehow the power input for the +5V regulator got removed, so the +5V
    doesn't run. Add the missing supply and fix the PCB trace.
    [avr-door-controller.kicad_pcb, avr-door-controller.sch]
2017-09-15 electronic: Move the door 1 open button to D7
    Pin D13 is connected to the status LED, so that can't be used for the
    door 1 open button, use D7 instead.
    [avr-door-controller.kicad_pcb, avr-door-controller.sch]
2017-09-15 firmware: trigger: Allow restarting an already running sequence
    Sometimes we want to restart an already running sequence, so fix
    stopping a running one, and don't forbid restarting.
    [trigger.c]
2017-09-15 firmware: trigger: Allow setting the trigger output to a fixed value
    [trigger.c]
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2017-09-15 firmware: door ctrl: Add the open button and status input
    Rework the door opening handling to support an external open button.
    While at it we also add the status input as button although it isn't
    handled yet.
    [door-controller.c]
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2017-09-15 firmware: boards: nano v3: Set the config for carrier rev 0
    We now finally have the "real" carrier with true PCB, however these
    have a slightly different pinning than the prototypes build on
    perfboards. To handle this correctly we would need to support
    different board revisions. Not a big deal but as we only used arduino
    nano v2 on the prototypes, and the new devices all get arduino nano v3,
    we just use this to differentiate the hardware versions for now.
    [arduino_nano_v3.c]
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2017-09-15 daemon: Rework the access record get/set methods
    * Use an integer type for every card field
    * Change the get result to use a 'pin' and/or 'card' field
    instead of the 'key' field.
    * Also allow passing a 'pin' or 'card' field to get a fully decoded
    record for pin+card records.
    * Make the 'card', 'pin' and 'doors' fields of the set_access_record
    optional.
2017-09-16 daemon: Add support for 'card+pin' to set_access_record
    We want get_access_record and set_access_record to be symetric, so add
    the missing support for 'card+pin' fields to set_access_record.
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2017-09-27 electronic: schematics: Add a relay to the modules library
    We need a simple single relay to replace the external relay modules.
2017-09-27 electronic: schematics: Integrate the external relay modules
    The external relais modules are bulky and annoying in a case, integrate
    them on the board.
    [avr-door-controller.sch]
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2017-09-27 electronic: schematics: Allow the board to run from 12V
    Add a step up module to allow generating the 24V from 12V instead of
    using 24V and a step down for the 12V. We still keep the 12V step down
    as we can easily make a PCB that will support both configurations.
    [avr-door-controller.sch]
2017-09-27 electronic: schematics: Move the power input back on the sheet
    [avr-door-controller.sch]
2017-09-27 electronic: schematics: Change the arduino fuse to 90mA
    90mA is enough and should really trip before the Arduino take too much
    damage.
    [avr-door-controller.sch]
2017-09-27 electronic: schematics: Annotate the new components
    [avr-door-controller.sch]
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2017-09-27 electronic: schematics: Set the footprints of the new components
    [avr-door-controller.sch]
2017-09-27 electronic: schematics: Use DO35 footprint for all the zener diodes
    It turned out to be easy to find DO35 zener dione with the proper
    rating. We used that on the rev 0 board but the holes are a bit too
    large which is annoying when soldering, so move to DO35 footprints.
    [avr-door-controller.sch]
2017-10-22 build: Add basic support for Travis CI
    Check that the firmware builds correctly for all supported boards
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2017-11-24 electronic: schematics: Update the jumper labels for the PCB
    To avoid using custom labels on the PCB just set the one we needs in
    the schematics. While at it also flip JP4 to match the pinout of JP3,
    that way they have the same orientation on the PCB.
    [avr-door-controller.sch]
2017-11-24 electronic: schematics: Add a jumper to select the input voltage
    To support both the step-up and step-down config we need to connect
    either the +12V or the +24V with the input voltage. This would mean
    adding a ratline on the PCB, which is not very nice. Instead we add a
    jumper footprint where one can easily solder a wire, along with the
    label it make it clearly visible which input voltage the board expect.
    [avr-door-controller.sch]
2017-11-25 electronic: footprint: Increase the pads size for the XM1584
    The pads on the XM1584 footprint were too small, raise the pads size
    from 1.524mm to 2mm to make soldering easier. While at it also round
    up the drill to 1mm and improve the + and - signs alignment.
2017-11-25 electronic: footprint: Fix the pads of the MT3608 to match the XM1584
    Better use the same pads on both modules, we will solder both in the
    same way.
2017-12-09 electronic: pcb: Completely rework the PCB for rev 2
    This is a completely new PCB with integrated relays, 24V step-up and
    enought space for the RTC module. It has been design to fit in an RND
    455-00119 case.
    [avr-door-controller.kicad_pcb]
2018-01-21 electronic: pcb: Increase the mounting holes size to 3mm
    The screw holes in the hounsing are a bit larger than expected. To
    properly attach the PCB we need 3mm holes instead of 2.5mm.
    [avr-door-controller.kicad_pcb]
2018-02-03 client: AVRDoorCtrl: UART: Fix parsing the command error code
    Parsing the error code of command from UART was broken as
    struct.unpack got the first byte of the buffer as argument instead the
    whole buffer.
    [AVRDoorCtrl.py]
2018-02-03 client: AVRDoorCtrl: Add some error message to validation exceptions
    Tell the user what was wrong when we abort because of bad arguments.
    [AVRDoorCtrl.py]
2018-02-03 client: AVRDoorCtrl: Fix the arguments for the ubus set_access command
    The `doors` parameter was missing from the parameters list of the ubus
    implementation of `set_access`.
    [AVRDoorCtrl.py]
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2018-02-21 client: admin: Fix the `group update` help strings and comment
    This code has been copied from the `group add` command but the help
    strings and comment haven't been properly updated, fix that.
    [avr-doors-admin.py]
2018-02-21 client: AVRDoorsDB: The Controller.uobject column doesn't exists
    The uobject column existed in early versions of the database, but it
    has been removed so it shouldn't be in the Controller class anymore.
    [AVRDoorsDB.py]
2018-02-21 client: admin: Fix the `controller list` command
    The `max_acl` field might be None but the list entry display didn't
    cope with this properly, fix that.
    [avr-doors-admin.py]
2018-02-21 client: db: Allow doors without a controller
    We might want to detach a door from its controller without having to
    delete it and loose all the related access records. This also allow to
    create doors before they are assigned to a controller.
    [avr-doors-admin.py]
2018-02-21 client: admin: Rework the `door add` and `door update` commands
    Rework the `door add` and `door update` commands now that the
    controller is optional. We make the controller and port optional for
    the `add` command and extend the `update` command to allow deleting
    these fields.
    [avr-doors-admin.py]
2018-02-21 client: AVRDoorsDB: Fix the string representation of DoorAccess
    The test for the `admin` field tested for `is True` which only work
    with python bool and not SQL boolean. Because of this the `(ADMIN)`
    flag never showed up for the door access records.
    [AVRDoorsDB.py]
2018-03-09 client: DB: Fix the where clause generation
    The generated where clause didn't include the provided condition as
    expected.
    [DB.py]
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2018-03-09 client: admin: Show all access that the user have in `user show`
    Add a new field to AVRDoorsDB.User that use the AllAccess view
    to get a full list of the user access, including those from the
    groups. Then rework `user show` to display this access list instead of
    just the personal door access.
    [AVRDoorsDB.py, avr-doors-admin.py]
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2019-10-21 client: db: Make sure the load method only match a single object
    As the user can pass a custom query to the contructor raise an error
    if the DB returns several rows.
    [DB.py]
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2019-10-21 eeprom: Fix the error code used in eeprom_get/set_access_record
    With the current implementation the only error that can happen is that
    the index is out of bound. However returning -EINVAL in this case is a
    bit too generic as the caller can't known the size of the storage.
    Return -ENOENT instead to allow caller to stop iterating while not
    ignoring other errors that might happen with another implementation.
2019-10-21 eeprom: Transparently handle invalid records
    Invalid records exists to make sure that unprogrammed eeprom are
    correctly handled. However it doesn't make sense to expose this to the
    user, so let eeprom_get_access_record() automatically turn invalid
    records into empty ones.
    While at it we can simplify eeprom_find_access_record() as it then
    doesn't need to handle the invalid record case.
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2020-10-01 client: ACRDoorCtrl: Fix the card+pin value return by ubus
    ubus doesn't properly encode u32 values in json as it return signed
    values. To work around this add filters on the 2 methods that can
    contain this field to convert any negative value back to unsigned as
    it should be.
    [AVRDoorCtrl.py]
2020-10-01 client: admin: Allow to set the database user
    This field was missing so one could only set the host and password but
    not the user, add that.
    [avr-doors-admin.py]
2020-10-01 daemon: Properly complete request in case of send error
    Errors in the send path were not handled, so the ubus method would not
    properly finish. Also handle the EOF case by returning an error.
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2020-10-01 daemon: Attach the uctx to the ubus method request
    Add the uctx to the ubus method request to avoid digging back through
    many layers to access the context from the top daemon object.
2025-08-11 door-ctrl: Pass the card ID and pin separately to the check function
    Combining the card ID and pin is an artifact of the limited storaged,
    so it doesn't make sense to do that in the door controller. This is
    also needed to be able to log the access events properly otherwise we
    can't tell the card number for card+pin access.
    [door-controller.c, main.c]
2025-08-11 firmware: Add a new API for deferred execution
    The event-queue API turned out to be a bit clumsy to use. The multi
    receiver capability has never been used and it use too much memory on
    the event handler side.
    The new work-queue API attempts to solve the same problem in a simpler
    way. Instead of events it allow to queue the execution of a function.
    To make it easy to use with the existing code the queued function use
    the same arguments as the event handlers.
    [work-queue.c]
2025-08-11 firmware: Replace the event-queue with the work-queue
    Use the new work queue instead of the event queue. This make the code
    a little bit simple and spare code and memory.
    [door-controller.c, main.c, uart-ctrl-transport.c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]
2025-08-11 client: DB: ObjectList: Reset the instances cache after loading
    Don't keep the old instances cache after (re)loading the list from the
    DB.
    [DB.py]
2025-08-11 client: DB: ObjectList: Use the object ID as cache entry
    We used the list index to access the instances cache, however this
    will not work if we allow adding or removing objects to the list.
    Use the object ID instead as that is stable.
    [DB.py]
2025-08-11 client: DB: Improve the exceptions text on load error
    When hitting a load error it is helpful to have some insight in the
    query that failed.
    [DB.py]
2025-08-11 client: DB: Improve error handling when loading objects
    Only clear the object if an error happen after we started modifying
    it, this keep the object as is if the error happen earlier.
    [DB.py]
2025-08-11 client: Fix the lookup of user access rights
    The current lookup just return the first access record found for the
    given user at the given door. It fails to check if the access record
    is valid at the current time, or if there is another record wich would
    provide admin rights.
    [AVRDoorsDB.py]
2025-08-11 firmware: Fix the arduino nano v3 MCU type
    The v3 has an atmega328p, which is basically identical to the
    atmega328, but we need the exact type for avrdude to be able to flash
    it.
    [atmega328p.h]
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2025-08-11 client: Fix the access record types name list
    It should be 'card+pin', and not 'pin+card', to match the firmware code.
    [AVRDoorCtrl.py]
2025-08-11 firmware: Rework the EEPROM storage to prepare for OTP pin
    To allow supporting OTP pins we need to rework the EEPROM storage as
    the trick to XOR the card and pin is not possible anymore. The new
    scheme doesn't need more space for the common case of only card or
    pin and allow for 3 type of PIN. Instead of xor'ing both data they are
    stored one after the other on the EEPROM. In memory the new records
    provide both the card and pin data for ease of use.
    A backward compatibility layer is included to avoid the need to change
    the API users right away. There is only limited support for pin+card
    through the compatibility layer, basically read-only, as the xor can't
    be undone.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
    [eeprom-types.h]
2025-08-11 client: Raise a TimeoutError when no data can be read from UART
    Use the correct exception when we stop receiving data from the UART.
    [AVRDoorCtrl.py]
2025-08-11 client: Convert common error codes to string
    Add an strerror() implementation so we can put a description of the
    error in the exception instead of just the errno code. We can't
    fallback on the libc here as the errno values are platform specific.
    [AVRDoorCtrl.py]
2025-08-11 client: Improve events handling
    Currently event received before a command reply would just be ignored.
    Add a queue to store them and a function to read them that start by
    emptying the queue, this way we don't drop any event. Then add a
    parsing function so we can display them in a human readable form.
    Finally improve the `show_events` function to skip over timeouts and
    stop on keyboard interrupt.
    [AVRDoorCtrl.py]
2025-08-11 client: ubus: Fix compatibility with newer OpenWrt versions
    In the past the JSON RPC frontend always returned a value, newer
    version only return an error code if there is no value. Handle this
    case and return an empty dict when there is no value to keep the same
    behavior.
2025-08-11 client: DB: Add server side OTP support
    Implementing OTP support in the firmware is major change that is still
    not finished. As a workaround we instead implement this feature in the
    database. For the rest of the software stack the OTP PIN are just
    normal PIN that are generated by the database. A big down side of this
    is the strain on the controllers EEPROM, so timeout shorter than 8 hours
    shouldn't be used. Also the controllers will get out of sync if they
    are offline for too long, or if the update cron job fails to run. On
    the positive side the controllers don't need an RTC module.
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2025-08-11 client: DB: Fix handling lists with a single column index
    The `id` of a database object is only a tuple if it has several index
    column. But the database cursor always return tuples, so when creating
    the items references list of a list we also need to convert tuples of
    lengths one to their first value.
    [DB.py]
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2025-08-11 client: Read the initial device descriptor
    The firmware now send the device descriptor as payload of the start
    event. Extend the serial handler `__init__` method to parse it and
    log the device version. If received, the device descriptor is cached so
    the `get_device_descriptor` method doesn't need to read it again.
    [AVRDoorCtrl.py]
2025-08-11 client: Add a custom exception for error messages
    Add a custom exception for error messages to allow for a better
    handling of the errors coming from the controller.
    [AVRDoorCtrl.py]
2025-08-11 client: Output proper JSON and handle errors
    Output the result a JSON so it can be easily processed by other tools.
    While at it also catch the controller error and report them using an
    error object and with the exit status code.
    [AVRDoorCtrl.py]
2025-08-11 client: Deduplicate the access record command line parsers
    The commands to handle the access records use the same arguments, use
    some function to add these arguments and avoid the code duplication.
    [AVRDoorCtrl.py]
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2025-08-11 firmware: Fix the format parameter passed to avr-size
    The current version of avr-size doesn't support the `-C` flag,
    use `--format=avr` instead.
2025-08-11 firmware: Add a controller config to store the OTP root key
    A root key is needed to derive the OTP secrets, it is stored in EEPROM
    before the door configuration. This loose some access record space so
    the opportunity is used to also remove unused fields in the door config.
    Two control commands are added to allow getting and setting the
    controller config. Unless build with debug the getter always return an
    empty key. Similarly the setter only overwrite the key if a new one is
    provided.
    [eeprom-types.h]
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2025-08-11 firmware: Avoid hanging when failling to send a command reply
    When `ctrl_transport_reply` fails to write out its paylod, for example
    because it is too large, it would switch to the
    `UART_CTRL_TRANSPORT_SYNC` state which prevent sending a new error
    reply. Update the condition to switch back to the
    `UART_CTRL_TRANSPORT_WAIT_FOR_REPLY` state instead to give the caller
    the chance to send an error reply.
    [uart-ctrl-transport.c]
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2025-08-11 daemon: Regularly ping the controller
    Regularly ping the controller if no command is sent for a while. If
    the ping command fails the transport is reset.
    [avr-door-controller-uart-transport.c]

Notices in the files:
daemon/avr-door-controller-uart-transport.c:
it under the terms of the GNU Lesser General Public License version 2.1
